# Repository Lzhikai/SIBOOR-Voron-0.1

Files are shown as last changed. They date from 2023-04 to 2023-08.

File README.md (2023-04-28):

# Tools to use
Download link：https://drive.google.com/drive/folders/1MjMfcktIfY5-pbY_Spfb1j_n9QCQVp6n?usp=sharing

# Fly3D GeminiV2.0-wiring

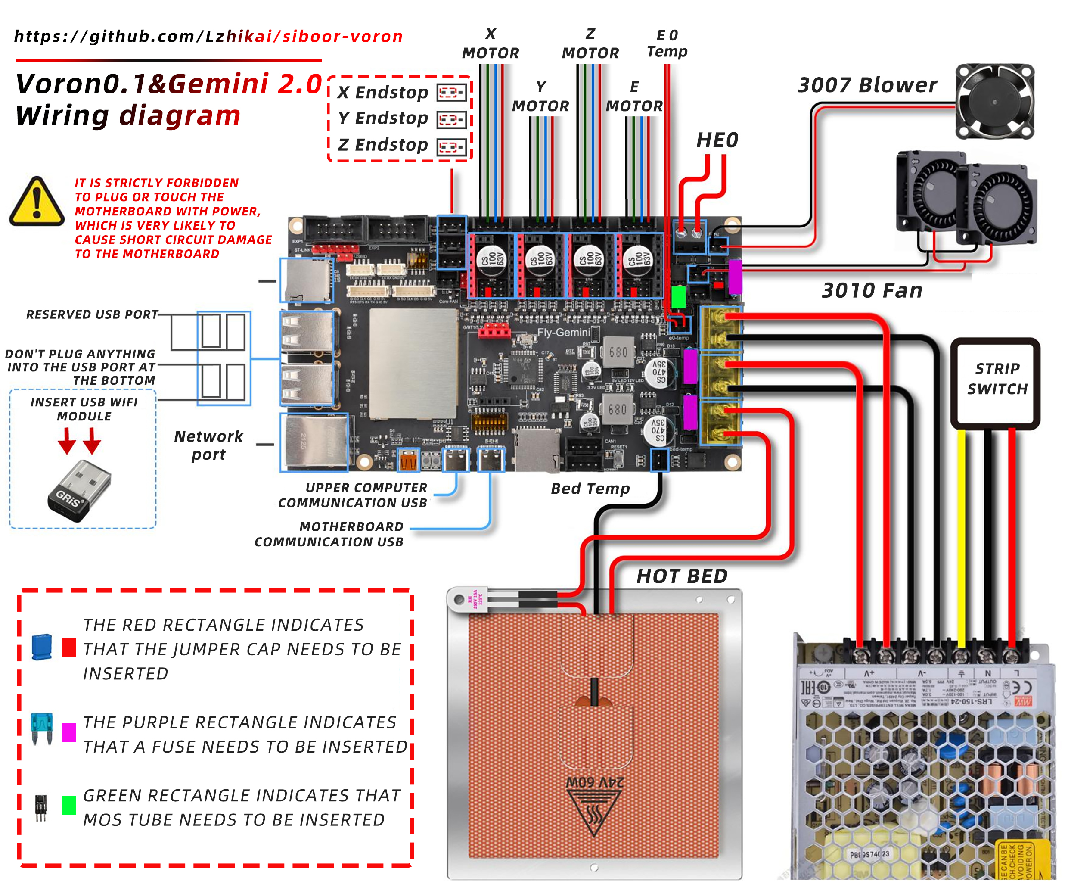
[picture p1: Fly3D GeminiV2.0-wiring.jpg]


# Fly3D GeminiV3.0-wiring

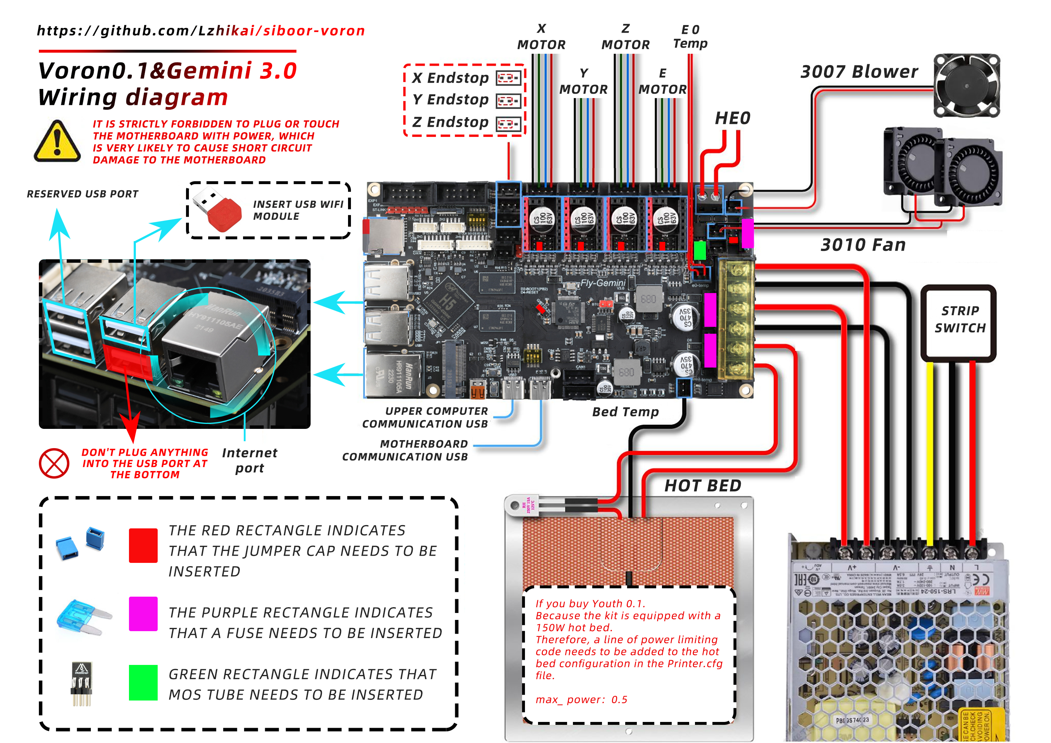
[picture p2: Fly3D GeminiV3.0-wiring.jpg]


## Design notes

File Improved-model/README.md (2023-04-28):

# 1-Youth Version 0.1 Cyan hot end housing modified tolerance
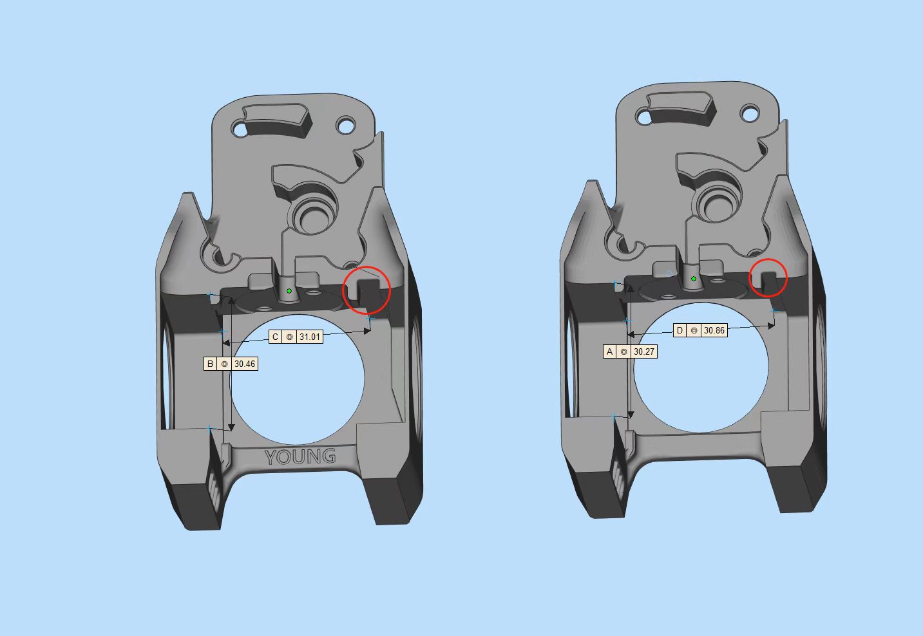
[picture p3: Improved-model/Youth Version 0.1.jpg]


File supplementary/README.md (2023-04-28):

# This guide covers the differences between the SIBOOR 0.1 kit and the original VORON0.1 tutorial, and includes instructions on wiring and debugging.  
# You can download and view the official PDF assembly tutorial of VORON here：[Voron-0.1/Manuals](https://github.com/VoronDesign/Voron-0/tree/Voron0.1/Manuals)  · [Voron-0/Manuals](https://github.com/VoronDesign/Voron-0/tree/Voron0.0/VORON-0/Manuals)  · GitHub

***Github SIBOOR V0.1 kit assembly manual instruction.***

* Page 10-11: In SIBOOR V0.1 kit, extrusion A and profile B are combined into one profile, both of which have been tapped and are common to each other. C profile and H profile are combined into one profile, both of which are drilled and tapped, which are common to each other.

* Page 14: The SIBOOR V0.1 kit uses the guide strip of purple PCB, so it does not need to use the printed parts and embedded M2 nut.

* Pages 15, 17 and 71: As described above, two purple PCBs are used as guide rail fixing strips to fix the MGN7 guide rail.

* Page 99: The SIBOOR V0.1 kit is already equipped with a soldered endstop, plug and play.

* Page 108: The hot end of the SIBOOR V0.1 Young Version requires a longer catheter (29.5mm). Make sure that the bearing is flush with the shaft, otherwise it will cause friction between the metal shaft and the motor. Place the side of the bearing flat on the table and press the white gear with both thumbs to make the bearing flush with the shaft.

* Page 111: Before installing the hot end to the printed parts, be sure to install the heating rod and thermal sensor in advance.

* Page 119: 2.5 × 6 self tapping screws are recommended here. Too long self tapping screw is easy to damage the printed parts.

* Page 126: In addition to using double-sided adhesive tape to fix the power supply, you can also choose to install two M3 × 6 screws on the reverse side  to fix the power supply.

* Page 127: In SIBOOR V0.1 kit, the step-down module is cancelled.

* Page 128: SIBOOR V0.1 kit, using a two in one Gemini motherboard, using four nylon posts and M3 × 8 Screws are fixed on the acrylic panel.

* Page 132-139: See the SIBOOR V0.1 kit supplementary instructions separatel



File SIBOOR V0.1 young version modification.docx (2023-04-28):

printer.cfg：

# BED

[heater_bed]

heater_pin: BED_OUT

sensor_pin: BED_TEMP

sensor_type: ATC Semitec 104GT-2

control: watermark

min_temp: 0

max_temp: 100 ##Limit the maximum temperature. If the set value is exceeded, an error will be reported and the operation will be stopped

max_power: 0.5 ##Limited heating power, 0. x represents percentage, 0.5 represents 50% power

The original FLY version is set to the maximum temperature of 200 degrees. The young version hot bed is heated faster, which may cause danger if the heating is too high. Now the maximum temperature is 100 degrees, and the heating power is 50%

[tmc2209 stepper_x]

uart_pin: X_CS

run_current: 0.800

interpolate: False

stealthchop_threshold:200 #Mute threshold to reduce motor running noise, recommended between 100-200

[tmc2209 stepper_y]

uart_pin: Y_CS

run_current: 0.800

interpolate: False

stealthchop_threshold:200 #Mute threshold to reduce motor running noise, recommended between 100-200

[tmc2209 stepper_z]

uart_pin: Z_CS

run_current: 0.4500 #The operating current of Axis Z is changed from 0.8 to 0.45. High current is not required for Axis Z to avoid serious heating

interpolate: False

[tmc2209 extruder]

uart_pin: E_CS

run_current: 0.4500 #The youth version is an ordinary motor. The current is changed from 0.8 to 0.45 to avoid serious heating

interpolate: False

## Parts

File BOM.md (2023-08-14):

# SIBOOR-Voron 0.1（Young） Bom list 
### This list only for reference.  
### Under special situations, parts will updated to same level and quality products.  
### If there has any changes, will update immediately here.
## SIBOOR-Voron 0.1（Young） Revision 1.1

| Category | Description | brand | Qty | update time |
|---|---|---|-----|---|
| Fasteners | 3x6x0.5 Shim Washer | / | 35  | 4/1/23 |
| | M2 Nut | / | 55  | 4/1/23 |
| | M3 Nut | / | 120 | 4/1/23 |
| | M2x6 BHCS/SHCS | / | 70  | 4/1/23 |
| | M2x6 FHCS | / | 10  | 4/1/23 |
| | M2x8 SHCS | / | 10  | 4/1/23 |
| | M2.5x6 | / | 5 | 4/1/23 |
| | M3x6 BHCS | / | 55  | 4/1/23 |
| | M3x8 BHCS | / | 100 | 4/1/23 |
| | M3x10 BHCS | / | 25  | 4/1/23 |
| | M3x12 BHCS | / | 25  | 4/1/23 |
| | M3x16 BHCS | / | 5 | 4/1/23 |
| | M3x25 BHCS | / | 10  | 4/1/23 |
| | M3x30 BHCS | / | 10  | 4/1/23 |
| | M3x35 BHCS | / | 30  | 4/1/23 |
| | M3x40 BHCS | / | 10  | 4/1/23 |
| | M2x10 Self Tapping Screws for Plastic | / | 15  | 4/1/23 |
| | M3 Brass heatstake inserts - short M3x5x4 | / | 50  | 4/1/23 |
| | M3 t-nut | / | 2 | 4/1/23 |
| | yellow die springs 8x4x25mm | / | 3 | 4/1/23 |
| | 6mm x 3mm Round Neodymium Magnets | / | 8 | 4/1/23 |
| | Bondtech BMG Extruder Kit | / | 1 | 4/1/23 |
| | MR85 Bearing | / | 2 | 4/1/23 |
| | Bowden Fitting | / | 2 | 4/1/23 |
| | small rubber feet | / | 4 | 4/1/23 |
| | M3 Lock Nut | / | 3 | 4/1/23 |
| Frame | EXTRUSION 15x15 200mm | SIBOOR | 16  | 4/1/23 |
| | EXTRUSION 15x15 100mm | SIBOOR | 3 | 4/1/23 |
| Electronics | LRS-150-24 | MEAN WELL | 1 | 4/1/23 |
| | Gemini V3 board | Mellow | 1 | 4/1/23 |
| | SanDisk MicroSD Card 32GB | Sandisk | 1 | 4/1/23 |
| | USB WIFI module | Tencent | 1 | 4/1/23 |
| | NEMA14 Stepper Motor 40Ncm | SIBOOR | 2 | 4/1/23 |
| | NEMA17 Stepper Motor w/ integrated lead screw 200mm T8x8 | SIBOOR | 1 | 4/1/23 |
| | NEMA14 36mm pancake Motor with 10 tooth gear | MOON‘S | 1 | 4/1/23 |
| | 3010 blower fans 24V | GEEK | 2 | 4/1/23 |
| | 3007 axial fan 24V | GEEK | 1 | 4/1/23 |
| | C13 Power Cord | / | 1 | 4/1/23 |
| | IEC320 C14 inlet | / | 1 | 4/1/23 |
| | Micro Switch | / | 1 | 4/1/23 |
| | v6 Hotend | SIBOOR | 1 | 4/1/23 |
| | 24V 40W Heater Cartridge (1M) | / | 1 | 4/1/23 |
| | Hotend thermistor(1M) | / | 1 | 4/1/23 |
| | High Flex Wire 20gauge  （35CM） | / | 2 | 4/1/23 |
| | 7mm x 7mm cable chain | / | 1 | 4/1/23 |
| | Nylon Cable Ties (1.8mm wide or smaller) | / | 50  | 4/1/23 |
| | Bowden Tube 4x2mm - 1m | / | 1 | 4/1/23 |
| | 3M 5952 VHB tape | / | 1 | 4/1/23 |
| Fasteners | F623-RS Bearing | / | 24  | 4/1/23 |
| Motion | MGN7H Linear Rail with Carriage - 150mm(nickel plated) | SIBOOR | 5 | 4/1/23 |
| | GT2 20T (5mm ID 6mm W) | SIBOOR | 2 | 4/1/23 |
| | GT2 Open Belt (6mm W) - 3000mm | GATES | 3 | 4/1/23 |
| Buildplate | 120×120×3mm 24V 150W heated bed | / | 1 | 4/1/23 |
| | Black Matte Magnetic Sticker 120×1220mm | / | 1 | 4/1/23 |
| Panels | Acrylic Sheet Clear - 212x230x2.5mm | unofficial version | 2 | 4/1/23 |
| | Acrylic Sheet Clear - 212x239x2.5mm | / | 1 | 4/1/23 |
| | Rear Panel 212mm x 248mm ( [See DXF](https://github.com/Lzhikai/SIBOOR-Voron-0.1/blob/main/SIBOOR%20V0.1%20(Youth%20Edition)%20cutting%20drawings.dwg)) | unofficial version | 1 | 4/1/23 |
| | Deck Panel 3mm thick ( [See DXF](https://github.com/Lzhikai/SIBOOR-Voron-0.1/blob/main/SIBOOR%20V0.1%20(Youth%20Edition)%20cutting%20drawings.dwg)) | unofficial version | 1 | 4/1/23 |
| | Motor Panel 3mm thick ( [See DXF](https://github.com/Lzhikai/SIBOOR-Voron-0.1/blob/main/SIBOOR%20V0.1%20(Youth%20Edition)%20cutting%20drawings.dwg)) | unofficial version | 1 | 4/1/23 |
| | Mid Panel 3mm thick ( [See DXF](https://github.com/Lzhikai/SIBOOR-Voron-0.1/blob/main/SIBOOR%20V0.1%20(Youth%20Edition)%20cutting%20drawings.dwg)) | / | 1 | 4/1/23 |
| | Tophat - Top Panel 180x211mm | / | 1 | 4/1/23 |
| | Tophat - Front/Rear Panel (See DXF) | / | 2 | 4/1/23 |
| | Tophat - Side Panel 206x73mm | / | 2 | 4/1/23 |
| Extrusion Tophat | Full set of prints（ABS） | SUNLU | 1 | 4/1/23 |

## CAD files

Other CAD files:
SIBOOR V0.1 (Youth Edition) cutting drawings.dwg

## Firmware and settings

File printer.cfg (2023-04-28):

[include fly_macros.cfg]

########################################
# Motherboard model
# Please modify it based on your motherboard model
# 请根据您的主板型号修改
########################################
#[include boards/FLY_GEMINI_V1.cfg]
#[include boards/FLY_GEMINI_V1.1.cfg]
[include boards/FLY_GEMINI_V3.cfg]

[mcu]
serial: /dev/Gemini_MCU

[mcu host]
serial: /tmp/klipper_host_mcu

[virtual_sdcard]
path: ~/gcode_files

[printer]
kinematics: corexy
max_velocity: 300
max_accel: 3000
max_z_velocity: 5
max_z_accel: 100


########################################
# Temp
########################################
[temperature_sensor FLY-Gemini]
sensor_type: temperature_host

[temperature_sensor FLY-MCU]
sensor_type: temperature_mcu

########################################
# Drives
########################################
[stepper_x]
step_pin: X_STEP
dir_pin: !X_DIR
enable_pin: !X_EN
microsteps: 16
rotation_distance: 40
endstop_pin: X_STOP
position_endstop: 120
position_max: 120
homing_speed: 40
step_pulse_duration: 0.000004
[stepper_y]
step_pin: Y_STEP
dir_pin: Y_DIR
enable_pin: !Y_EN
microsteps: 16
rotation_distance: 40
endstop_pin: Y_STOP
position_endstop: 120
position_max: 120
homing_speed: 40
step_pulse_duration: 0.000004
[stepper_z]
step_pin: Z_STEP
dir_pin: !Z_DIR
enable_pin: !Z_EN
microsteps: 16
rotation_distance: 8
endstop_pin: Z_STOP
position_endstop: 0.5
position_max: 120

[extruder]
step_pin: E_STEP
dir_pin: E_DIR
enable_pin: !E_EN
microsteps: 16
rotation_distance: 23
gear_ratio: 50:10   
nozzle_diameter: 0.400
filament_diameter: 1.750
heater_pin: HEAT
sensor_pin: HEAT_TEMP
sensor_type: ATC Semitec 104GT-2
control: pid
pid_Kp: 22.2
pid_Ki: 1.08
pid_Kd: 114
min_temp: 0
max_temp: 350
min_extrude_temp: 10


########################################
# BED
########################################
[heater_bed]
heater_pin: BED_OUT
sensor_pin: BED_TEMP
sensor_type: ATC Semitec 104GT-2
control: watermark
min_temp: 0
max_temp: 100
max_power: 0.5

########################################
# FANs
########################################
[fan]
pin: FAN0
#cycle_time: 0.50

#[fan_generic fan1]
#pin: FAN1



########################################
# TMC2208 configuration./2209/2225
########################################
[tmc2209 stepper_x]
uart_pin: X_CS
run_current: 0.850
interpolate: False
stealthchop_threshold:200

[tmc2209 stepper_y]
uart_pin: Y_CS
run_current: 0.850
interpolate: False
stealthchop_threshold:200

[tmc2209 stepper_z]
uart_pin: Z_CS
run_current: 0.4500
interpolate: False

[tmc2209 extruder]
uart_pin: E_CS
run_current: 0.4500
interpolate: False

#打印开始    
[gcode_macro PRINT_START]
#   Use PRINT_START for the slicer starting script - please customize for your slicer of choice
description: 开始打印
gcode:
    G90
    M107
    M82
    G28
    G1 Z20 F3000
    G92 E0
    G1 X110 Y0.5 F2000
    G1 Z0.28 F400
    G1 X30 Y0.5 E18 F1000
    G1 Z0.5 F200
    G92 E0

    #G28                            ; home all axes
    #G1 Z20 F3000                   ; move nozzle away from bed
    

#打印结束
[gcode_macro PRINT_END]
#   Use PRINT_END for the slicer ending script - please customize for your slicer of choice
gcode:
    M400                           ; wait for buffer to clear
    G92 E0                         ; zero the extruder
    G1 E-4.0 F3600                 ; retract filament
    G91                            ; relative positioning

    #   Get Boundaries
    {% set max_x = printer.configfile.config["stepper_x"]["position_max"]|float %}
    {% set max_y = printer.configfile.config["stepper_y"]["position_max"]|float %}
    {% set max_z = printer.configfile.config["stepper_z"]["position_max"]|float %}

    #   Check end position to determine safe direction to move
    {% if printer.toolhead.position.x < (max_x - 20) %}
        {% set x_safe = 20.0 %}
    {% else %}
        {% set x_safe = -20.0 %}
    {% endif %}

    {% if printer.toolhead.position.y < (max_y - 20) %}
        {% set y_safe = 20.0 %}
    {% else %}
        {% set y_safe = -20.0 %}
    {% endif %}

    {% if printer.toolhead.position.z < (max_z - 2) %}
        {% set z_safe = 2.0 %}
    {% else %}
        {% set z_safe = max_z - printer.toolhead.position.z %}
    {% endif %}

    G0 Z{z_safe} F3600             ; move nozzle up
    G0 X{x_safe} Y{y_safe} F20000  ; move nozzle to remove stringing
    TURN_OFF_HEATERS
    M107                           ; turn off fan
    G90                            ; absolute positioning
    G0 X60 Y{max_y} F3600          ; park nozzle at rear
    SET_SKEW CLEAR=1

########################################
# TMC5160 configuration
########################################
#[tmc5160 stepper_x]
#cs_pin: X_CS
##spi_bus: spi3  ##Gemini v1.1
##diag1_pin: X_STOP
#run_current: 0.800
#interpolate: False

#[tmc5160 stepper_y]
#cs_pin: Y_CS
#spi_bus: spi3  ##Gemini v1.1
##diag1_pin: Y_STOP
#run_current: 0.800
#interpolate: False

#[tmc5160 stepper_z]
#cs_pin: Z_CS
##spi_bus: spi3  ##Gemini v1.1
##diag1_pin: Z_STOP
#run_current: 0.650
#interpolate: False

#[tmc5160 extruder]
#cs_pin: E_CS
##spi_bus: spi3  ##Gemini v1.1
#run_current: 0.800
#interpolate: False



########################################
 #BLTouch
########################################
#[bltouch]
#sensor_pin: ^PROBE
#control_pin: SERVO
#pin_move_time: 0.680
#x_offset: 0.0
#y_offset: 2.3
#z_offset: 2.2
#speed: 70

#[safe_z_home]
#home_xy_position: 105,105



########################################
 #Mini 12864 LCD
########################################
#[display]
#lcd_type: uc1701
#cs_pin: EXP1_3
#a0_pin: EXP1_4
#rst_pin: EXP1_5
#contrast: 63
#encoder_pins: ^EXP2_5, ^!EXP2_3
#click_pin: ^!EXP1_2
##spi_bus: spi1

#####适用于FLY Mini12864
#[neopixel fly_mini12864]
#pin: EXP1_6
#chain_count: 3
#initial_RED: 0.1
#initial_GREEN: 0.5
#initial_BLUE: 0.0
#color_order: RGB
